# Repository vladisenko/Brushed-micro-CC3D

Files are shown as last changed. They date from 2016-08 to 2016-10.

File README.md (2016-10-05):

# Brushed micro CC3D
Small size version of the CC3D flight controller. It's developed for the 90mm carbon frame (CF-01). PCB is contain receiver based on A7105, FlySky compatible. Also board have mosfet drivers for brushed motors. 

PCB with "2oz 0.8mm" option from [OSH Park](https://oshpark.com/shared_projects/dTEgwpc5).

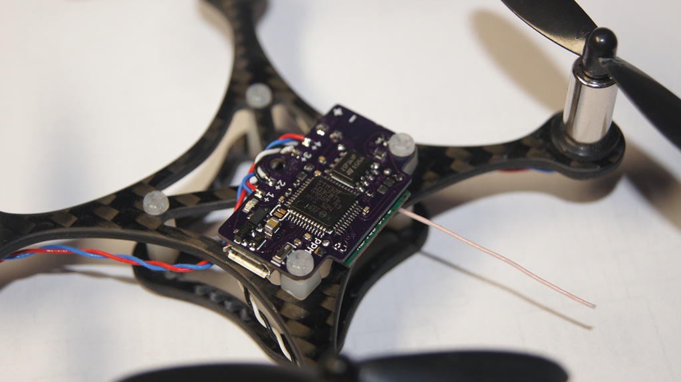
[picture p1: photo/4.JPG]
pcb on frame


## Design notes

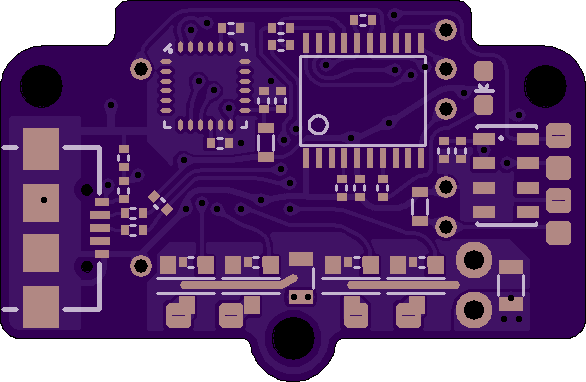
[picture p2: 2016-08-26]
hw/bottom.png

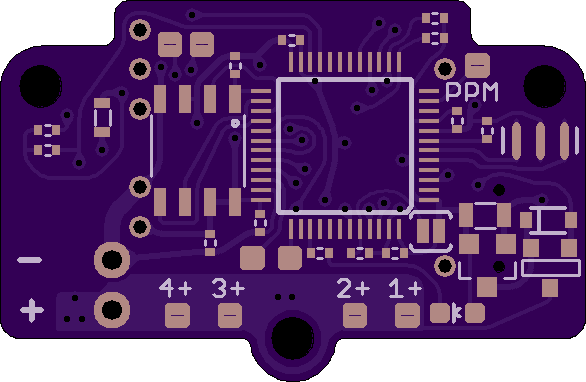
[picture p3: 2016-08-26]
hw/top.png

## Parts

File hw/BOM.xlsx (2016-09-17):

Part | Value | Package
C1 | u47 | 0402
C2 | u47 | 0402
C3 | 47n | 0402
C4 | 0u1 | 0402
C5 | 2n2 50v | 0402
C6 | 47n | 0402
C7 | u47 | 0805
C8 | 47n | 0402
C9 | u1 | 0402
C10 | u1 | 0402
C11 | 47n | 0402
C12 | 0u1 | 0402
C13 | 0u1 | 0402
C14 | 0u1 | 0402
C15 | 0u1 | 0402
C16 | 0u1 | 0603
C17 | 0u1 | 0402
C18 | 2u2 | 0805
C19 | 2u2 | 0805
D1 | BAT54 | SOD-323
FB1 |  | 0603
FB2 |  | 0603
IC1 | MPU-6000 | QFN-24
IC2 | MS5611 | LGA8
IC3 | XC6206P332 | SOT23
IC4 | STM32F103CBT6 | LQFP48
IC5 | M25P16 | SO08
IC6 | STM32F030F4T6 | TSSOP-20
JP1 | BAT | 1X02
LED1 |  | LED-0603
LED2 |  | LED-0603
Q1 | Si2312 | SOT-23
Q2 | Si2312 | SOT-23
Q3 | Si2312 | SOT-23
Q4 | Si2312 | SOT-23
Q5 | AO3401 | SOT-23
R1 | 22R | 0402
R2 | 22R | 0402
R3 | 1k5 | 0402
R4 | 2k2 | 0402
R5 | 10k | 0402
R6 | 2k2 | 0402
R7 | 10k | 0402
R8 | 15k | 0402
R9 | DNP | 0402
R10 | 1k | 0402
R11 | 680R | 0402
R12 | 510R | 0402
R13 | 510R | 0402
R14 | 10k | 0402
R15 | 1k | 0402
R16 | 680R | 0402
R17 | 10k | 0402
R18 | 10k | 0402
R19 | 10k | 0402
R20 | 10k | 0402
U$1 | microUSB
U$2 |  | XL7105-SY-B
Y1 | CSTCE8.000M

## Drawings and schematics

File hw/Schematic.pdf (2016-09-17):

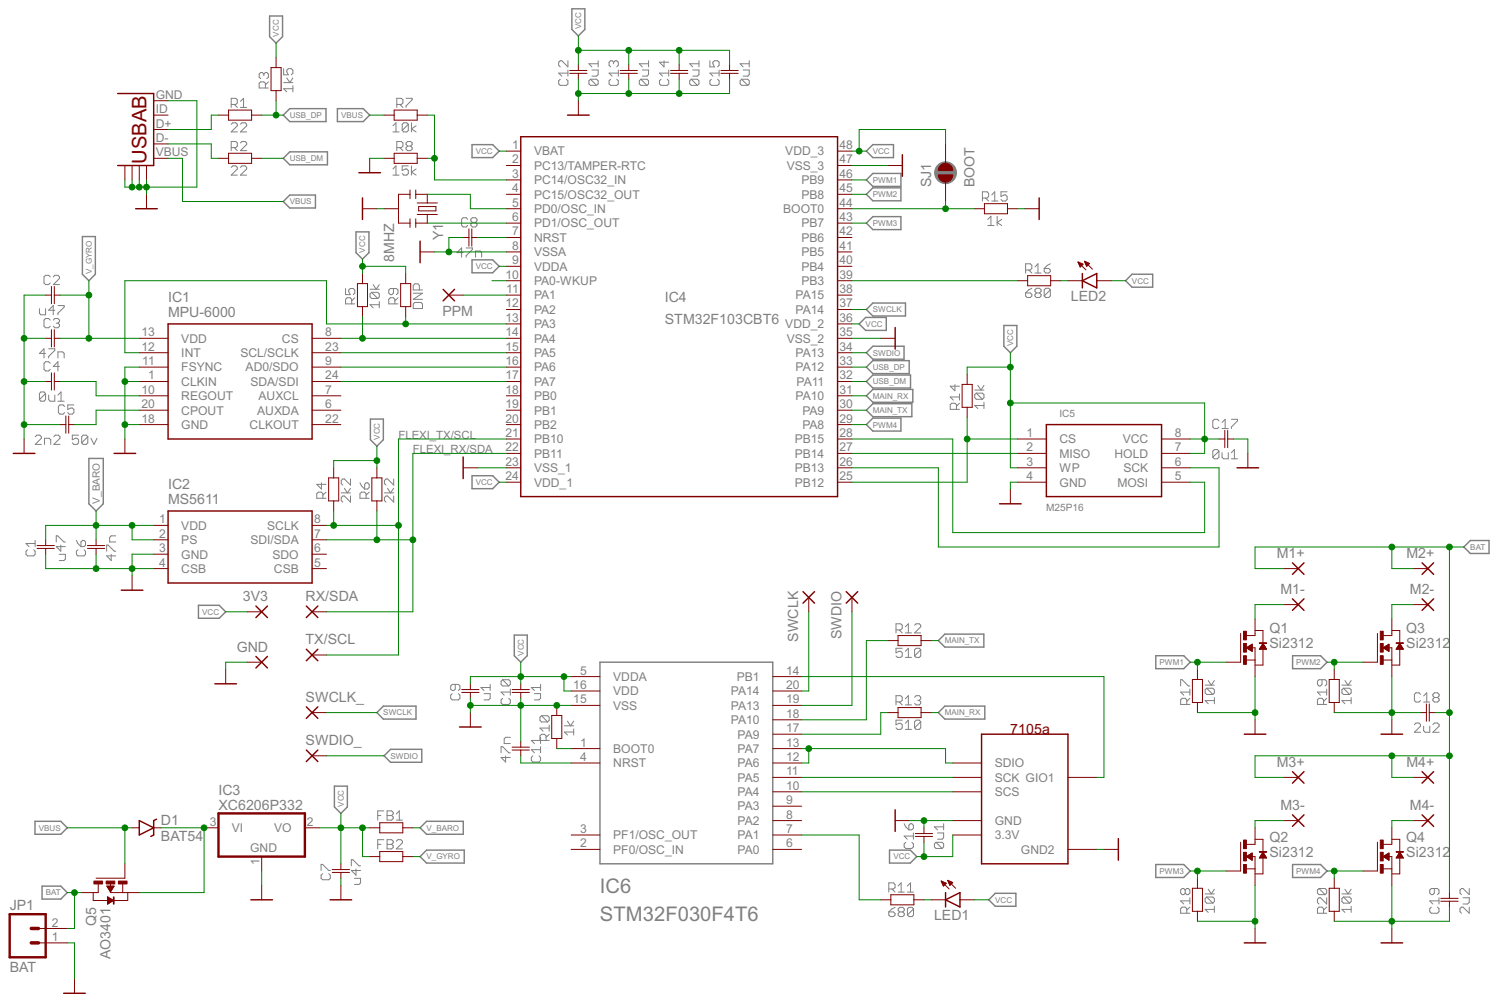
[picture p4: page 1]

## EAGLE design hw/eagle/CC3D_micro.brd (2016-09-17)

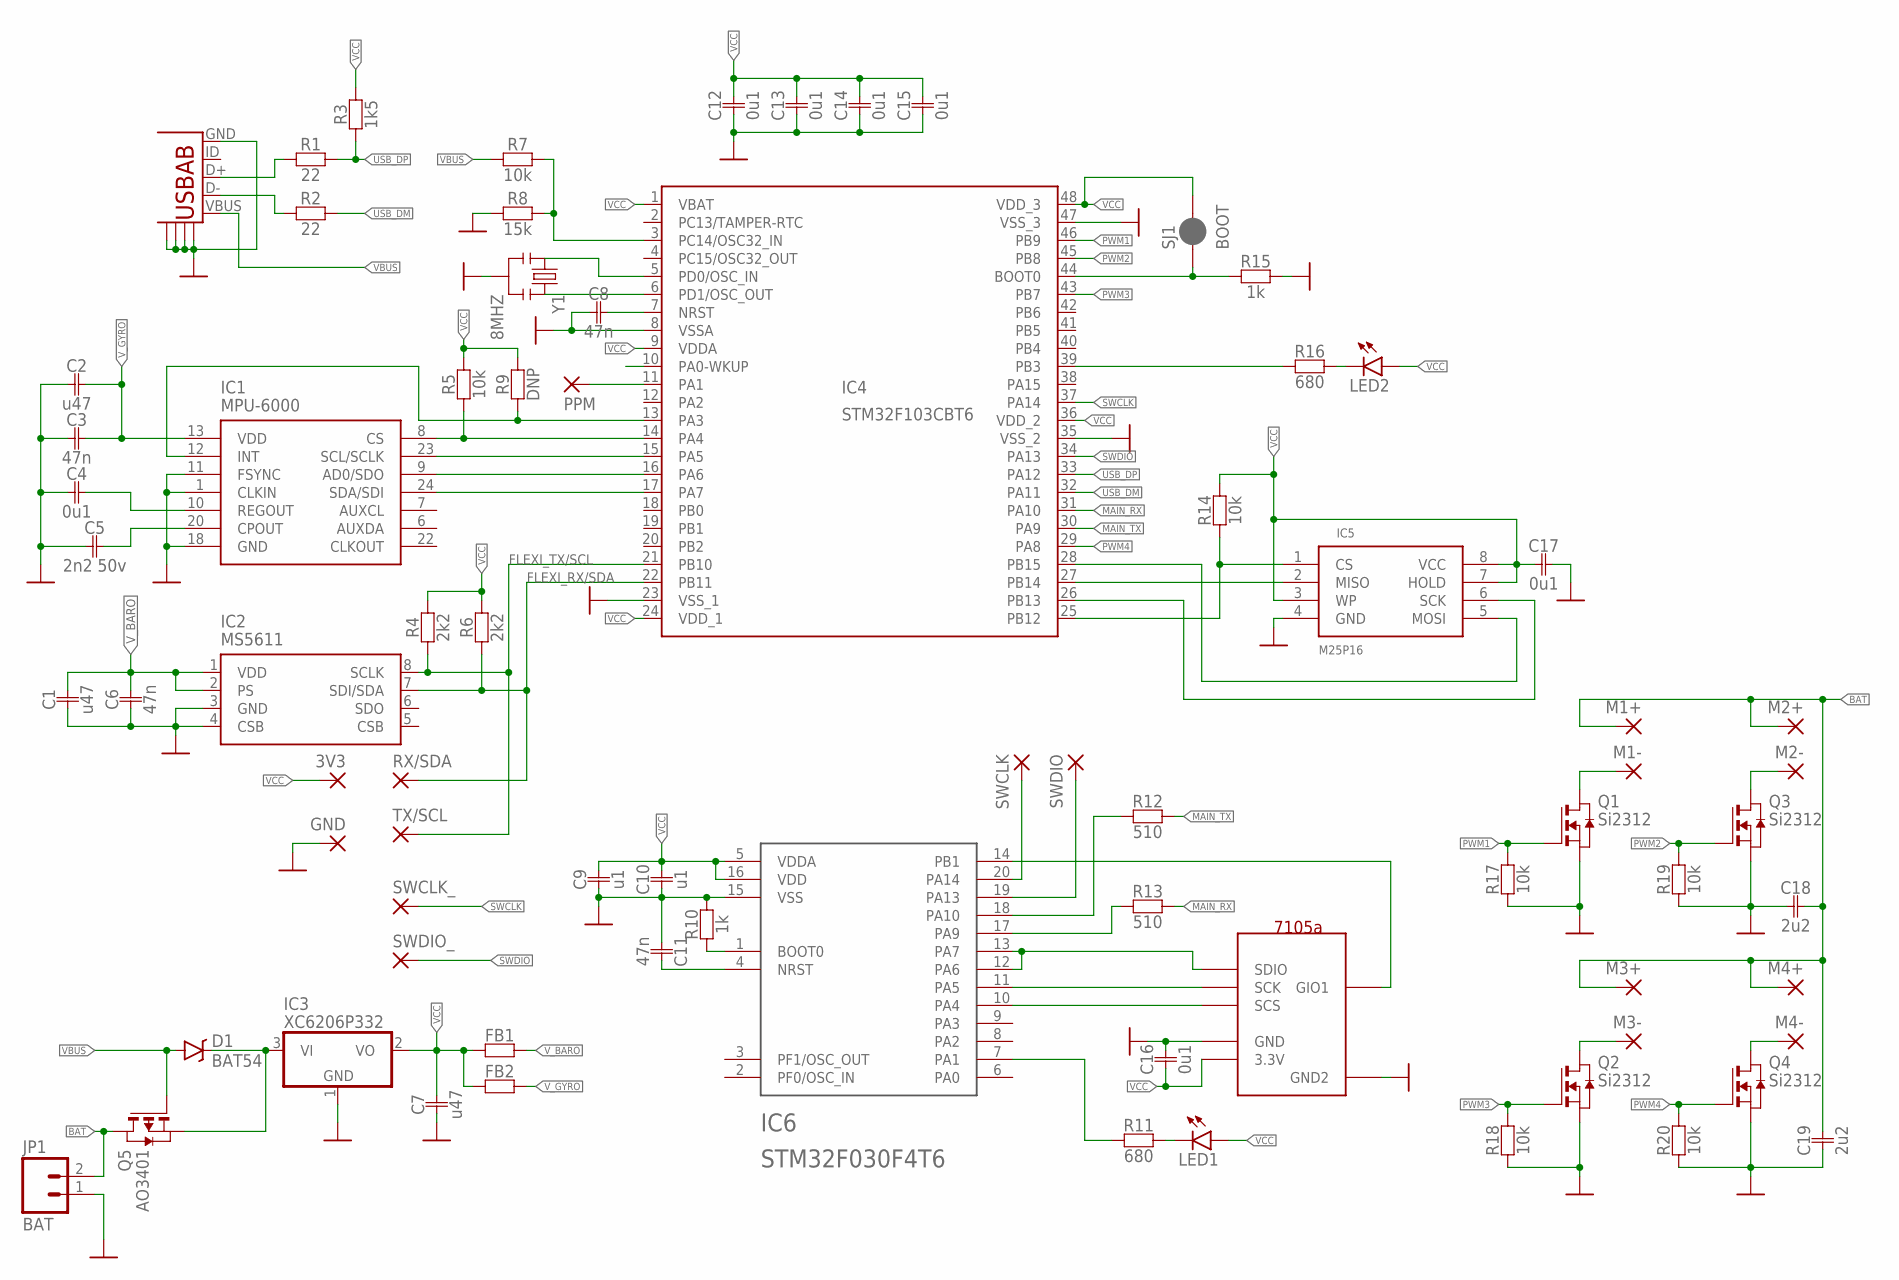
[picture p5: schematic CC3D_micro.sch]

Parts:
3V3: SMD2; SMD1,27-2,54
C1, C2: u47; 0402
C3, C6, C8, C11: 47n; 0402
C4, C12, C13, C14, C15, C17: 0u1; 0402
C5: 2n2 50v; 0402
C7: u47; 0805
C9, C10: u1; 0402
C16: 0u1; 0603
C18, C19: 2u2; 0805
D1: BAT54; SOD-323
FB1, FB2: R0603; 0603
GND: SMD2; SMD1,27-2,54
IC1: MPU-6000; QFN-24-TESTING
IC2: MS5611; LGA8
IC3: XC6206P332; SOT23
IC4: STM32F103CBT6; LQFP48
IC5: M25P16; SO08
IC6: STM32F030F4T6; TSSOP-20
JP1: BAT; 1X02_NO_SILK
LED1, LED2: LED0603; LED-0603
M1+, M1-, M2+, M2-, M3+, M3-, M4+, M4-: SMD2; SMD1,27-2,54
PPM: SMD2; SMD1,27-2,54
Q1, Q2, Q3, Q4: Si2312; SOT-23
Q5: AO3401; SOT-23
R1, R2: 22; 0402
R3: 1k5; 0402
R4, R6: 2k2; 0402
R5, R7, R14, R17, R18, R19, R20: 10k; 0402
R8: 15k; 0402
R9: DNP; 0402
R10, R15: 1k; 0402
R11, R16: 680; 0402
R12, R13: 510; 0402
RX/SDA: SMD2; SMD1,27-2,54
SJ1: BOOT; PAD-JUMPER-2-NC_BY_PASTE_YES_SILK
SWCLK: SMD2; SMD1,27-2,54
SWCLK_: SMD2; SMD1,27-2,54
SWDIO: SMD2; SMD1,27-2,54
SWDIO_: SMD2; SMD1,27-2,54
TX/SCL: SMD2; SMD1,27-2,54
U$1: microUSB; UNTITLED_USB-AB-MICRO-SMD
U$2: XL7105-SL-B-TH; XL7105-SY-B
Y1: 8MHZ; RESONATOR-SMD

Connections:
BAT: C18.P$2, C19.P$2, JP1.2, M1+.1, M2+.1, M3+.1, M4+.1, Q5.1 (D)
FLEXI_RX/SDA: IC2.7 (SDI/SDA), IC4.22 (PB11), R6.P$1, RX/SDA.1
FLEXI_TX/SCL: IC2.8 (SCLK), IC4.21 (PB10), R4.P$1, TX/SCL.1
GND: C1.P$1, C2.P$1, C3.P$1, C4.P$1, C5.P$1, C6.P$1, C7.P$1, C8.P$1, C9.P$1, C10.P$2, C11.P$1, C12.P$1, C13.P$1, C14.P$1, C15.P$1, C16.P$2, C17.P$2, C18.P$1, C19.P$1, GND.1, IC1.1 (CLKIN), IC1.11 (FSYNC), IC1.18 (GND), IC2.3 (GND), IC2.4 (CSB), IC3.1 (GND), IC4.8 (VSSA), IC4.23 (VSS_1), IC4.35 (VSS_2), IC4.47 (VSS_3), IC5.4 (GND), IC6.15 (VSS), JP1.1, Q1.2 (S), Q2.2 (S), Q3.2 (S), Q4.2 (S), R8.P$2, R10.P$2, R15.P$2, R17.P$1, R18.P$1, R19.P$1, R20.P$1, U$1.GND, U$1.GND@1, U$1.GND@2, U$1.GND@3, U$1.GND@4, U$2.P$2 (GND), U$2.P$6 (GND2), Y1.2
M1+: M1-.1, Q1.1 (D)
M2+: M2-.1, Q3.1 (D)
M3+: M3-.1, Q2.1 (D)
M4+: M4-.1, Q4.1 (D)
MAIN_RX: IC4.31 (PA10), R13.P$2
MAIN_TX: IC4.30 (PA9), R12.P$2
unnamed: IC1.12 (INT), IC4.13 (PA3), R9.P$1
unnamed: IC1.8 (CS), IC4.14 (PA4), R5.P$1
unnamed: IC1.23 (SCL/SCLK), IC4.15 (PA5)
unnamed: IC1.9 (AD0/SDO), IC4.16 (PA6)
unnamed: IC1.24 (SDA/SDI), IC4.17 (PA7)
unnamed: IC6.1 (BOOT0), R10.P$1
unnamed: IC4.25 (PB12), IC5.1 (CS), R14.P$1
unnamed: IC4.26 (PB13), IC5.6 (SCK)
unnamed: IC4.27 (PB14), IC5.2 (MISO)
unnamed: IC4.28 (PB15), IC5.5 (MOSI)
unnamed: IC4.6 (PD1/OSC_OUT), Y1.3
unnamed: IC6.14 (PB1), U$2.P$7 (GIO1)
unnamed: IC4.39 (PB3), R16.P$1
unnamed: LED2.C, R16.P$2
unnamed: IC4.3 (PC14/OSC32_IN), R7.P$2, R8.P$1
unnamed: R2.P$2, U$1.D-
unnamed: IC4.44 (BOOT0), R15.P$1, SJ1.1
unnamed: R1.P$2, U$1.D+
unnamed: IC6.10 (PA4), U$2.P$3 (SCS)
unnamed: IC6.11 (PA5), U$2.P$4 (SCK)
unnamed: LED1.C, R11.P$2
unnamed: IC6.12 (PA6), IC6.13 (PA7), U$2.P$5 (SDIO)
unnamed: IC6.17 (PA9), R13.P$1
unnamed: IC6.18 (PA10), R12.P$1
unnamed: IC6.19 (PA13), SWDIO.1
unnamed: IC6.20 (PA14), SWCLK.1
unnamed: IC6.7 (PA1), R11.P$1
unnamed: C4.P$2, IC1.10 (REGOUT)
unnamed: IC4.5 (PD0/OSC_IN), Y1.1
unnamed: C5.P$2, IC1.20 (CPOUT)
unnamed: IC4.11 (PA1), PPM.1
unnamed: D1.C, IC3.3 (VI), Q5.2 (S)
unnamed: C8.P$2, IC4.7 (NRST)
unnamed: C11.P$2, IC6.4 (NRST)
PWM1: IC4.46 (PB9), Q1.3 (G), R17.P$2
PWM2: IC4.45 (PB8), Q3.3 (G), R19.P$2
PWM3: IC4.43 (PB7), Q2.3 (G), R18.P$2
PWM4: IC4.29 (PA8), Q4.3 (G), R20.P$2
SWCLK: IC4.37 (PA14), SWCLK_.1
SWDIO: IC4.34 (PA13), SWDIO_.1
USB_DM: IC4.32 (PA11), R2.P$1
USB_DP: IC4.33 (PA12), R1.P$1, R3.P$2
VBUS: D1.A, Q5.3 (G), R7.P$1, U$1.VBUS
VCC: 3V3.1, C7.P$2, C9.P$2, C10.P$1, C12.P$2, C13.P$2, C14.P$2, C15.P$2, C16.P$1, C17.P$1, FB1.P$1, FB2.P$1, IC3.2 (VO), IC4.1 (VBAT), IC4.9 (VDDA), IC4.24 (VDD_1), IC4.36 (VDD_2), IC4.48 (VDD_3), IC5.3 (WP), IC5.7 (HOLD), IC5.8 (VCC), IC6.5 (VDDA), IC6.16 (VDD), LED1.A, LED2.A, R3.P$1, R4.P$2, R5.P$2, R6.P$2, R9.P$2, R14.P$2, SJ1.2, U$2.P$1 (3.3V)
V_BARO: C1.P$2, C6.P$2, FB1.P$2, IC2.1 (VDD), IC2.2 (PS)
V_GYRO: C2.P$2, C3.P$2, FB2.P$2, IC1.13 (VDD)

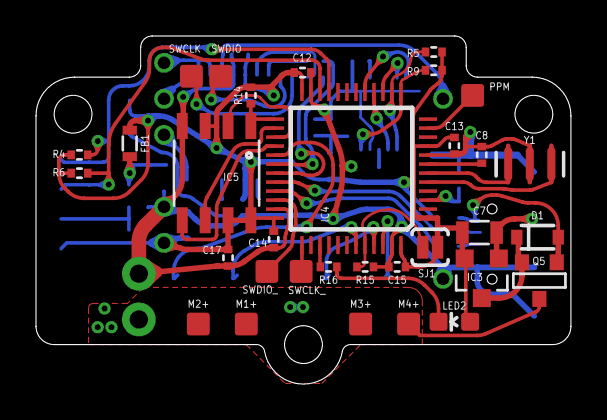
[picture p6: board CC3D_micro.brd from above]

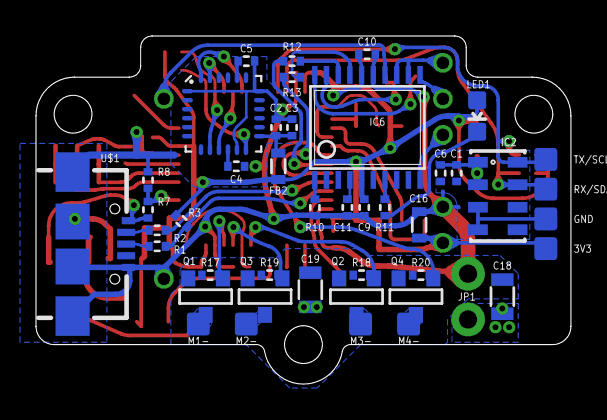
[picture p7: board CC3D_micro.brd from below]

Board: 2 copper layers, 29.7 x 19.3 mm, 77 parts (45 on the bottom side), 56 nets.

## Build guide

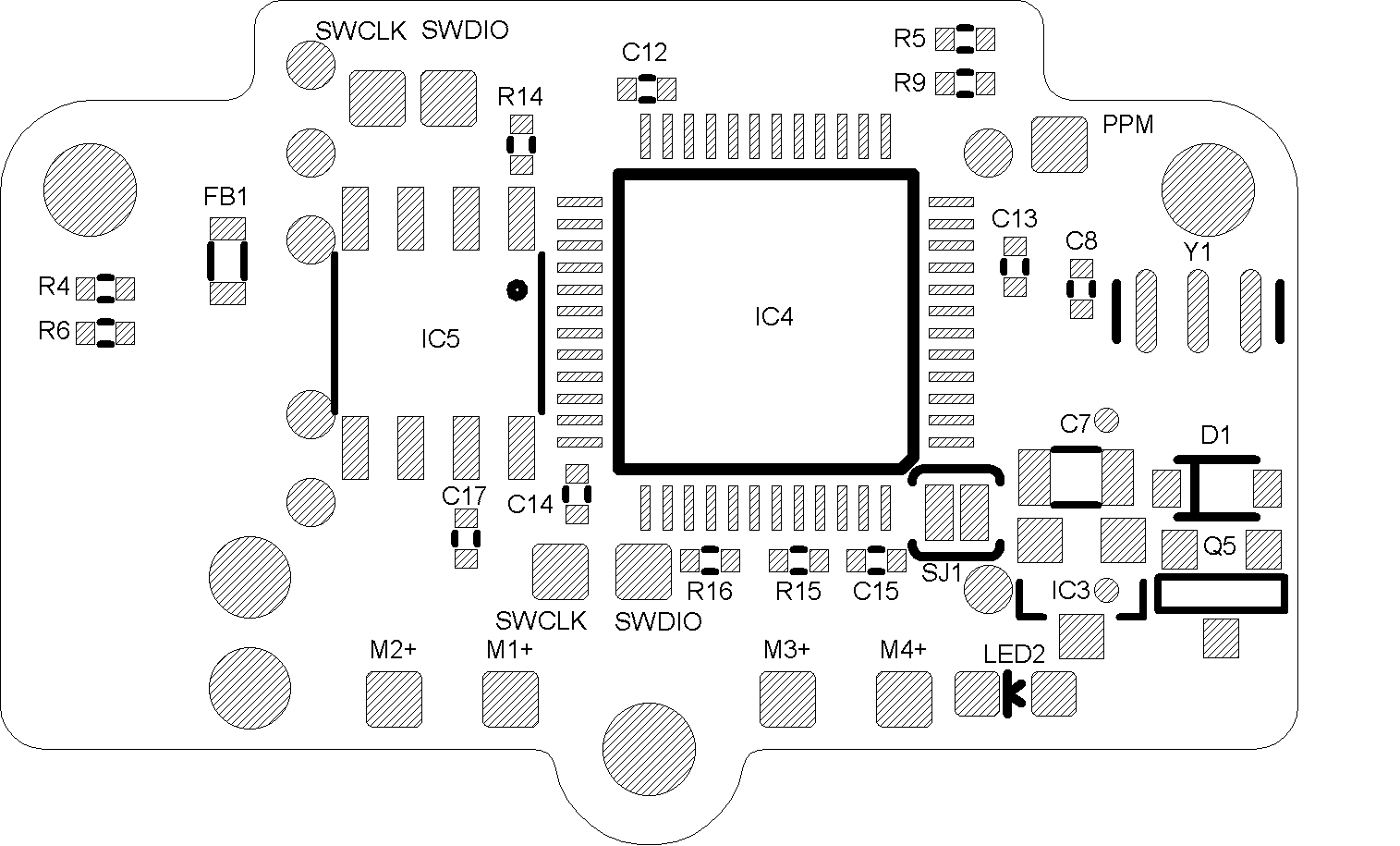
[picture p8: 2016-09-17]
hw/top_assembly.png

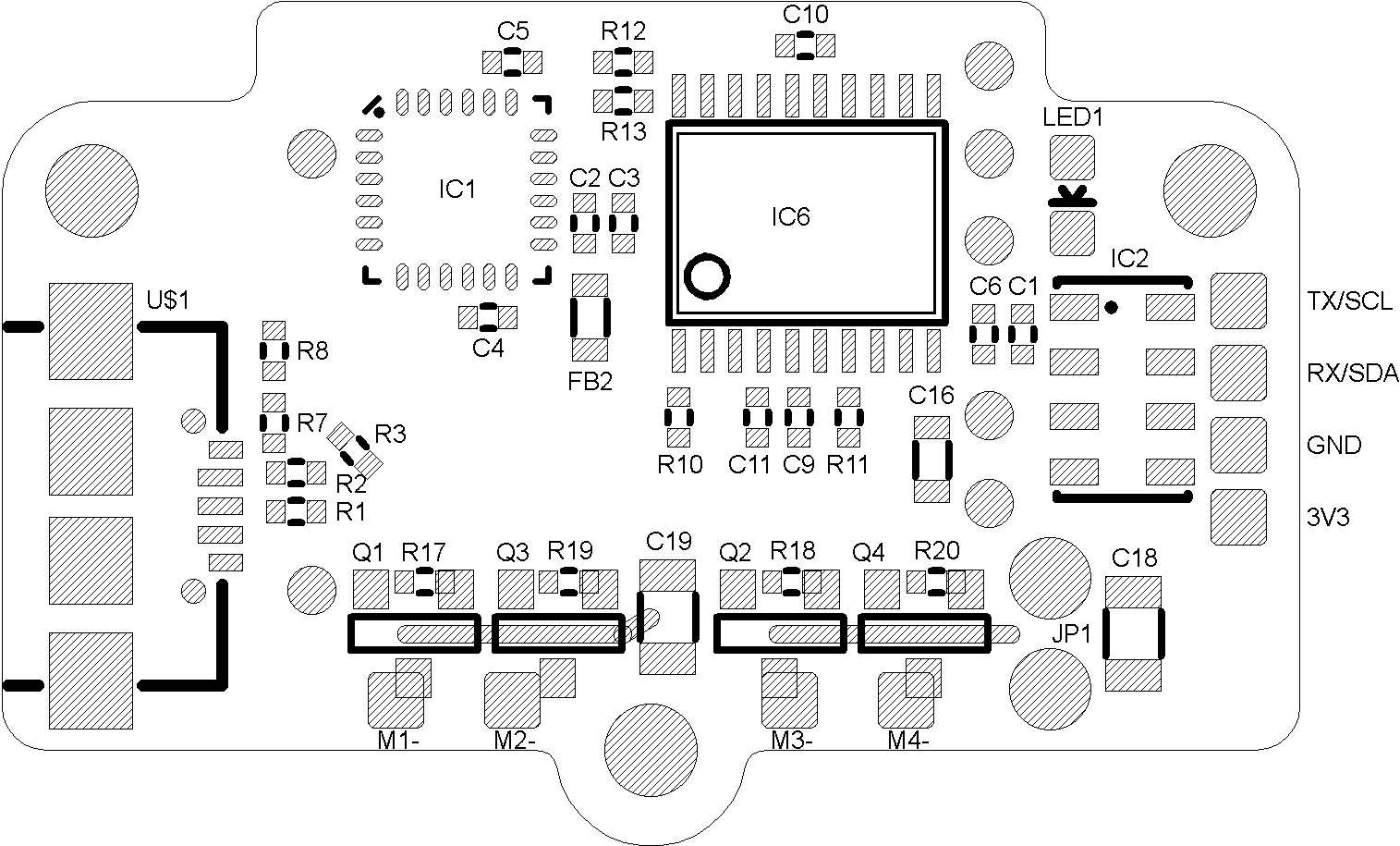
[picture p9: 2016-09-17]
hw/bottom_assembly.png

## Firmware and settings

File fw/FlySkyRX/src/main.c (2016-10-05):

/*
FlySky compatible receiver with DSM-like output. Tested with LibrePilot CC3D,
Cleanflight and Betaflight.
After the first turn on the receiver automatically switches to bind mode.
For manual binding pin PA13 and PA14 must be closed before power up. 

Sources:
	http://www.rcgroups.com/forums/showthread.php?t=1921870
	http://www.parkflyer.ru/ru/blogs/view_entry/12740/
	https://developer.mbed.org/users/d34d/code/A7105TxRx/
*/


#include "stm32f0xx.h"
#include "A7105.h"
#include "dsm.h"
#include "flash.h"

#define FLYSKY_PACKET_SIZE		21

#define TICK_US					100
#define US(us)					(((us) + TICK_US/2)/TICK_US)
#define MS(ms)					(US(1000UL*ms))	

#define LED_ON()				do { GPIOA->BSRR = GPIO_BSRR_BR_1; } while(0)
#define LED_OFF()				do { GPIOA->BSRR = GPIO_BSRR_BS_1; } while(0)


uint8_t DSMFrame[DSM_FRAME_LENGTH];

const uint8_t A7105_regs[] = {
  0xff, 0x42, 0x00, 0x14, 0x00, 0xff, 0xff , 0x00, 0x00, 0x00, 0x00, 0x01, 0x21, 0x05, 0x00, 0x50,
  0x9e, 0x4b, 0x00, 0x02, 0x16, 0x2b, 0x12, 0x00, 0x62, 0x80, 0x80, 0x00, 0x0a, 0x32, 0xc3, 0x0f,
  0x13, 0xc3, 0x00, 0xff, 0x00, 0x00, 0x3b, 0x00, 0x17, 0x47, 0x80, 0x03, 0x01, 0x45, 0x18, 0x00,
  0x01, 0x0f, 0xff,
};

const uint8_t tx_channels[16][16] = {
  {0x0a, 0x5a, 0x14, 0x64, 0x1e, 0x6e, 0x28, 0x78, 0x32, 0x82, 0x3c, 0x8c, 0x46, 0x96, 0x50, 0xa0},
  {0xa0, 0x50, 0x96, 0x46, 0x8c, 0x3c, 0x82, 0x32, 0x78, 0x28, 0x6e, 0x1e, 0x64, 0x14, 0x5a, 0x0a},
  {0x0a, 0x5a, 0x50, 0xa0, 0x14, 0x64, 0x46, 0x96, 0x1e, 0x6e, 0x3c, 0x8c, 0x28, 0x78, 0x32, 0x82},
  {0x82, 0x32, 0x78, 0x28, 0x8c, 0x3c, 0x6e, 0x1e, 0x96, 0x46, 0x64, 0x14, 0xa0, 0x50, 0x5a, 0x0a},
  {0x28, 0x78, 0x0a, 0x5a, 0x50, 0xa0, 0x14, 0x64, 0x1e, 0x6e, 0x3c, 0x8c, 0x32, 0x82, 0x46, 0x96},
  {0x96, 0x46, 0x82, 0x32, 0x8c, 0x3c, 0x6e, 0x1e, 0x64, 0x14, 0xa0, 0x50, 0x5a, 0x0a, 0x78, 0x28},
  {0x50, 0xa0, 0x28, 0x78, 0x0a, 0x5a, 0x1e, 0x6e, 0x3c, 0x8c, 0x32, 0x82, 0x46, 0x96, 0x14, 0x64},
  {0x64, 0x14, 0x96, 0x46, 0x82, 0x32, 0x8c, 0x3c, 0x6e, 0x1e, 0x5a, 0x0a, 0x78, 0x28, 0xa0, 0x50},
  {0x50, 0xa0, 0x46, 0x96, 0x3c, 0x8c, 0x28, 0x78, 0x0a, 0x5a, 0x32, 0x82, 0x1e, 0x6e, 0x14, 0x64},
  {0x64, 0x14, 0x6e, 0x1e, 0x82, 0x32, 0x5a, 0x0a, 0x78, 0x28, 0x8c, 0x3c, 0x96, 0x46, 0xa0, 0x50},
  {0x46, 0x96, 0x3c, 0x8c, 0x50, 0xa0, 0x28, 0x78, 0x0a, 0x5a, 0x1e, 0x6e, 0x32, 0x82, 0x14, 0x64},
  {0x64, 0x14, 0x82, 0x32, 0x6e, 0x1e, 0x5a, 0x0a, 0x78, 0x28, 0xa0, 0x50, 0x8c, 0x3c, 0x96, 0x46},
  {0x46, 0x96, 0x0a, 0x5a, 0x3c, 0x8c, 0x14, 0x64, 0x50, 0xa0, 0x28, 0x78, 0x1e, 0x6e, 0x32, 0x82},
  {0x82, 0x32, 0x6e, 0x1e, 0x78, 0x28, 0xa0, 0x50, 0x64, 0x14, 0x8c, 0x3c, 0x5a, 0x0a, 0x96, 0x46},
  {0x46, 0x96, 0x0a, 0x5a, 0x50, 0xa0, 0x3c, 0x8c, 0x28, 0x78, 0x1e, 0x6e, 0x32, 0x82, 0x14, 0x64},
  {0x64, 0x14, 0x82, 0x32, 0x6e, 0x1e, 0x78, 0x28, 0x8c, 0x3c, 0xa0, 0x50, 0x5a, 0x0a, 0x96, 0x46},
};


volatile uint32_t Tick = 0;

uint8_t rcv[FLYSKY_PACKET_SIZE];
uint8_t txid[5];
uint8_t chanrow;
uint8_t chancol;
uint8_t chanoffset;
uint8_t channel;

void HWInit (void);
void DelayTick (uint32_t t);

uint8_t CheckJumper (void);
uint32_t GetTick (void);

void FlySkyInit (void);
void FlySkyBind (void);
void NextChannel (void);


int main (void)
{
	uint32_t time_last_dms = 0;
	uint32_t time_last_pkg_flysky = 0;
	uint32_t time_led = 0;
	uint32_t id;
	
	uint32_t timeout_flysky = US(1600);
	uint16_t lost_pkg_flysky = 0;
		
	uint8_t bind;
	uint8_t have_new_pkg_flysky = 0;
	uint8_t led_state = 0, led_flashing = 0;
	
	
	HWInit();
	
	bind = CheckJumper();
	
	DelayTick(MS(100));
	DSMInit();
	FlySkyInit();
	
	LoadTXID(txid, sizeof(txid));
	
	if (bind || (txid[0] != 0xAA))
	{
		FlySkyBind();
		SaveTXID(txid, sizeof(txid));
		while(1);
	}
  
	id = (txid[1] | ((uint32_t)txid[2] << 8) | ((uint32_t)txid[3] << 16) | ((uint32_t)txid[4] << 24));
	chanrow = id & 0x0F;
	chanoffset = ((id & 0xF0) >> 4) + 1;
	chancol = 0;
	if (chanoffset > 9) chanoffset = 9; //from sloped soarer findings, bug in flysky protocol
	
	time_last_pkg_flysky = GetTick();
	
	while (1)
	{
	
		if (GIO_GET() == 0)
		{
			if ((A7105ReadReg(A7105_00_MODE) & (1 << 5)) != 0)			// CRC error
			{
				A7105Strobe(A7105_RST_RDPTR);
				A7105Strobe(A7105_RX);			
			}
			else
			{
				A7105ReadFIFO(&rcv[0], FLYSKY_PACKET_SIZE);
				if ((rcv[1] == txid[1]) && (rcv[2] == txid[2]) && (rcv[3] == txid[3]) && (rcv[4] == txid[4]))
				{
					time_last_pkg_flysky = GetTick();
					NextChannel();
					have_new_pkg_flysky = DSM_TIMEOUT;
					lost_pkg_flysky = 0;
					timeout_flysky = (US(1600));
				}
			}
		}
		
			
		if ((GetTick() - time_last_pkg_flysky) >= timeout_flysky)
		{
			NextChannel();	
			time_last_pkg_flysky = GetTick();
				
			if (lost_pkg_flysky < UINT16_MAX) lost_pkg_flysky++;
			timeout_flysky = (lost_pkg_flysky < 120) ? (US(1500)) : (US(1600));
		}
		
		
		if ((GetTick() - time_last_dms) > MS(11))
		{
			if (have_new_pkg_flysky)
			{
				uint8_t ch;
				
				have_new_pkg_flysky--;
				
				time_last_dms = GetTick();
			
				DSMFrame[0] = 0;
#if DSM_11BIT
				DSMFrame[1] = 0x12;
#else
				DSMFrame[1] = 0x01;				
#endif				
				
				for (ch = 0; ch < DSM_CHANNELS_PER_FRAME; ch++)
				{
					uint32_t tmp;
					time_last_dms = GetTick();
						
					tmp = (rcv[2*ch + 6] << 8) | rcv[2*ch + 5];
					if (tmp > 1000) tmp -= 1000; else tmp = 0;									// todo: check value
#if DSM_11BIT
					tmp = (tmp * 2047 + 500)/1000;				
					tmp = (tmp & 0x07FF) | (ch << 11);
#else
					tmp = (tmp * 1023 + 500)/1000;				
					tmp = (tmp & 0x03FF) | (ch << 10);				
#endif
					DSMFrame[2*ch + 2]  = (tmp >> 8) & 0x00FF;
					DSMFrame[2*ch + 3]  = tmp & 0x00FF;
				}
				DSMSend(&DSMFrame[0], sizeof(DSMFrame));
			}
			else
			{
				led_flashing = 1;
			}
			
		}
		
		
		if (led_flashing && (!led_state))
		{
			led_flashing = 0;
			led_state = 1;
		}
		
		
		switch(led_state)
		{
			case 0:
			break;

			case 1:
				LED_ON();
				time_led = GetTick();
				led_state++;
			break;
			
			case 2:
				if ((GetTick() - time_led) > MS(100)) led_state++;
			break;	
				
			case 3:
				LED_OFF();
				time_led = GetTick();
				led_state++;
			break;
				
			case 4:
				if ((GetTick() - time_led) > MS(500)) led_state = 0;
			break;
			
			default:
			break;		
		}

		__WFI();
	}
}


void SysTick_Handler (void)
{
	Tick++;
}


void HWInit (void)
{
	SystemCoreClockUpdate();
	SysTick_Config(SystemCoreClock/(1000000UL/TICK_US));
	
	RCC->AHBENR |= RCC_AHBENR_GPIOAEN;
	
	GPIOA->MODER =	(1U << 1*2) |			// PA1 - LED - GPout,
					(1U << 4*2) |			// PA4 - CS A7105 - GPout,
					(2U << 5*2) |			// PA5 - SCK A7105 - AF,
					(2U << 6*2) |			// PA6 - DIO A7105 - AF,
					(2U << 7*2) |			// PA7 - DIO A7105 - AF,
					(2U << 13*2) |			// PA13 - SDWIO - AF,
					(2U << 14*2) ;			// PA14 - SWCLK - AF.
	
	GPIOA->OTYPER = (1 << 1);				// PA1 - LED - open drain
	
	GPIOA->PUPDR =	(2U << 0*2) |			// PA0 - Pull-down,
					(2U << 2*2) |			// PA2 - Pull-down,
					(2U << 3*2) |			// PA3 - Pull-down,
					(2U << 6*2) |			// PA6 - Pull-down,
					(2U << 8*2) |			// PA8 - Pull-down,
					(2U << 10*2) |			// PA10 - Pull-down,
					(2U << 11*2) |			// PA11 - Pull-down,
					(2U << 12*2) |			// PA12 - Pull-down,
					(2U << 15*2);			// PA15 - Pull-down.
					
	GPIOA->OSPEEDR =(3U << 5*2) |			// PA5 - SCK A7105 - high speed,
					(3U << 7*2) |			// PA7 - DIO A7105 - high speed,
					(3U << 13*2);			// PA13 - SDWIO - high speed.
	

	GPIOA->BSRR = GPIO_BSRR_BS_4 | GPIO_BSRR_BR_7 | GPIO_BSRR_BR_5;
	
	
	RCC->AHBENR |= RCC_AHBENR_GPIOBEN;
	GPIOB->PUPDR =	(1U << 1*2);			// PB1 - Pull-up.

	
	RCC->APB2ENR |= RCC_APB2ENR_SPI1EN;
	SPI1->CR1 = 0;
	SPI1->CR2 = SPI_CR2_FRXTH |				// RXNE event is generated if the FIFO level is greater than or equal to 1/4 (8-bit)
				SPI_CR2_DS_0 |				// Data Size: 0b0111 - 8 bit
				SPI_CR2_DS_1 |
				SPI_CR2_DS_2;
	SPI1->CR1 = SPI_CR1_MSTR |
				SPI_CR1_SPE |				// Peripheral enabled
				SPI_CR1_SSI |				// Internal slave select
				SPI_CR1_SSM ;				// Software slave management
}



uint8_t CheckJumper (void)
{
	uint8_t res = 0;
	
	RCC->AHBENR |= RCC_AHBENR_GPIOAEN;
	
	GPIOA->MODER = 0x10000000 | (GPIOA->MODER & ~0x3C000000);	// PA13 - GP in,
																// PA14 - GP out.
	if ((GPIOA->IDR & (1<<13)) == 0) res = 1;
	
	GPIOA->MODER = 0x28000000 | (GPIOA->MODER & ~0x3C000000);	// PA13 - SDWIO - AF,
																// PA14 - SWCLK - AF.
	return res;
}



void DelayTick (uint32_t t)
{
	uint32_t start = Tick;
	while ( (uint32_t)(Tick - start) < t);
}



uint32_t GetTick (void)
{
	return Tick;
}	



void FlySkyBind (void)
{
	uint16_t binded = 0;
	uint16_t led_state = 0;
	uint32_t time_led_bl = 0;
	
	A7105SetChannel(0x00);												// binding listen on channel 0

	while(binded == 0)
	{
					
		if (GIO_GET() == 0)
		{
			if ((A7105ReadReg(A7105_00_MODE) & (1 << 5)) != 0)			// CRC error
			{
				A7105Strobe(A7105_RST_RDPTR);
				A7105Strobe(A7105_RX);			
			}
			else
			{
				uint16_t i;
				
				A7105ReadFIFO(&rcv[0], FLYSKY_PACKET_SIZE);
				if (rcv[0] == 0xAA)
				{
					for(i = 0; i < sizeof(txid); i++)
					{
						txid[i] = rcv[i];
					}
					binded = 1;
				}
			}
		}	
		
		if ((GetTick() - time_led_bl) > MS(1000))
		{
			time_led_bl = GetTick();
			led_state = !led_state;
			if (led_state)
				LED_ON();
			else
				LED_OFF();
			
		}
	}
	LED_ON();
}



void FlySkyInit (void)
{
	uint16_t i;
	
	A7105SoftReset();
	A7105WriteID(0x5475c52A);
	
	for (i = 0; i < 0x33; i++)
	{
		if (A7105_regs[i] != 0xff)
		{
			A7105WriteReg((a7105_reg_t)i, A7105_regs[i]);
		}
	}
 	A7105Strobe(A7105_STANDBY);
	A7105WriteReg(A7105_02_CALC, 0x01);
	while (A7105ReadReg(A7105_02_CALC) != 0){}
	A7105ReadReg(A7105_22_IF_CALIB_I);
		
	A7105WriteReg(A7105_24_VCO_CURCAL, 0x13);
	A7105WriteReg(A7105_25_VCO_SBCAL_I, 0x09);
	A7105Strobe(A7105_STANDBY);
}



void NextChannel (void)
{
	channel = tx_channels[chanrow][chancol] - chanoffset;
	chancol++;
	chancol	&= 0x0F;
	A7105SetChannel(channel);
}

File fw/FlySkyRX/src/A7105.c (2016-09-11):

#include "stm32f0xx.h"
#include "A7105.h"


static __inline uint8_t SPISend (uint8_t data)
{
	while ((SPI1->SR & SPI_SR_TXE) == 0){}
	*(uint8_t *)&(SPI1->DR) = (uint8_t) data;
	while ((SPI1->SR & SPI_SR_RXNE) == 0){} 	
	return (uint8_t) SPI1->DR;		
}



void A7105Strobe (a7105_state_t st)
{
	A7105_SEL();
	SPISend((uint8_t)st);
	while ((SPI1->SR & SPI_SR_BSY) != 0){}
	A7105_DESEL();
}


void A7105WriteReg (a7105_reg_t reg, uint8_t data)
{
	A7105_SEL();
	SPISend((uint8_t)reg);
	SPISend(data);
	while ((SPI1->SR & SPI_SR_BSY) != 0){}
	A7105_DESEL();
} 



uint8_t A7105ReadReg (a7105_reg_t reg)
{
	uint8_t res;
	
	A7105_SEL();
	SPISend(((uint8_t)reg) | 0x40);	

	GPIOA->MODER &= ~GPIO_MODER_MODER7_1;
	res = SPISend(0xFF);
	A7105_DESEL();
	GPIOA->MODER |= GPIO_MODER_MODER7_1;
	
	return res;
} 



static void A7105WriteRegMul (a7105_reg_t reg, uint8_t *data, uint16_t num)
{
	uint16_t i;
	
	A7105_SEL();
	SPISend((uint8_t)reg);
	for (i = 0; i < num; i++)
	{
		SPISend(*data++);
	}
	while ((SPI1->SR & SPI_SR_BSY) != 0){}
	A7105_DESEL();
}


static void A7105ReadRegMul (a7105_reg_t reg, uint8_t *data, uint16_t num)
{
	uint16_t i;
	uint8_t tmp;
	
	A7105_SEL();
	SPISend(((uint8_t)reg) | 0x40);	

	GPIOA->MODER &= ~GPIO_MODER_MODER7_1;
	for (i = 0; i < num; i++)
	{
		tmp = SPISend(0xFF);
		*data++ = tmp;
	}	

	A7105_DESEL();
	GPIOA->MODER |= GPIO_MODER_MODER7_1;
}


void A7105ReadFIFO (uint8_t *data, uint8_t num)
{
	if(num > 64) num = 64;
	A7105ReadRegMul (A7105_05_FIFO_DATA, data, num);
}


void A7105WriteID(uint32_t ida)
{
	uint8_t data[4];
	data[0] = (ida>>24)&0xff;
	data[1] = (ida>>16)&0xff;
	data[2] = (ida>>8)&0xff;
	data[3] = (ida>>0)&0xff;
	A7105WriteRegMul (A7105_06_ID_DATA, &data[0], sizeof(data));
}

uint32_t A7105ReadID (void)
{
	uint32_t id;
	uint8_t data[4];
	
	A7105ReadRegMul (A7105_06_ID_DATA, &data[0], sizeof(data));
	id  = data[0] << 24;
	id |= data[1] << 16;
	id |= data[2] << 8;
	id |= data[3] << 0;
	return id;
}


void A7105SoftReset (void)
{
	A7105WriteReg(A7105_00_MODE, 0x00);
}


void A7105SetChannel (uint8_t chan)
{
	A7105Strobe(A7105_STANDBY);
	A7105Strobe(A7105_RST_RDPTR);
	A7105WriteReg(A7105_0F_CHANNEL, chan);
	A7105Strobe(A7105_RX);
}

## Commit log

2016-08-26 add hw
    [CC3D_micro.brd, CC3D_micro.sch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]
2016-09-11 hw v0.2
    [CC3D_micro.brd, CC3D_micro.sch]
2016-09-11 update schematic
2016-09-17 add BOM
    [BOM.xlsx, CC3D_micro.brd, CC3D_micro.sch]

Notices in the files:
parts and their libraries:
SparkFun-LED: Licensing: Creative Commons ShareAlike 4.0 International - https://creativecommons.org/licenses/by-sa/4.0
